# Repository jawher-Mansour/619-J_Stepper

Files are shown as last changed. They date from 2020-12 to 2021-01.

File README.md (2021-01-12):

<div align="center"><h1 style="font-family: courier;" align="center">619-J_Stepper</h1></div>
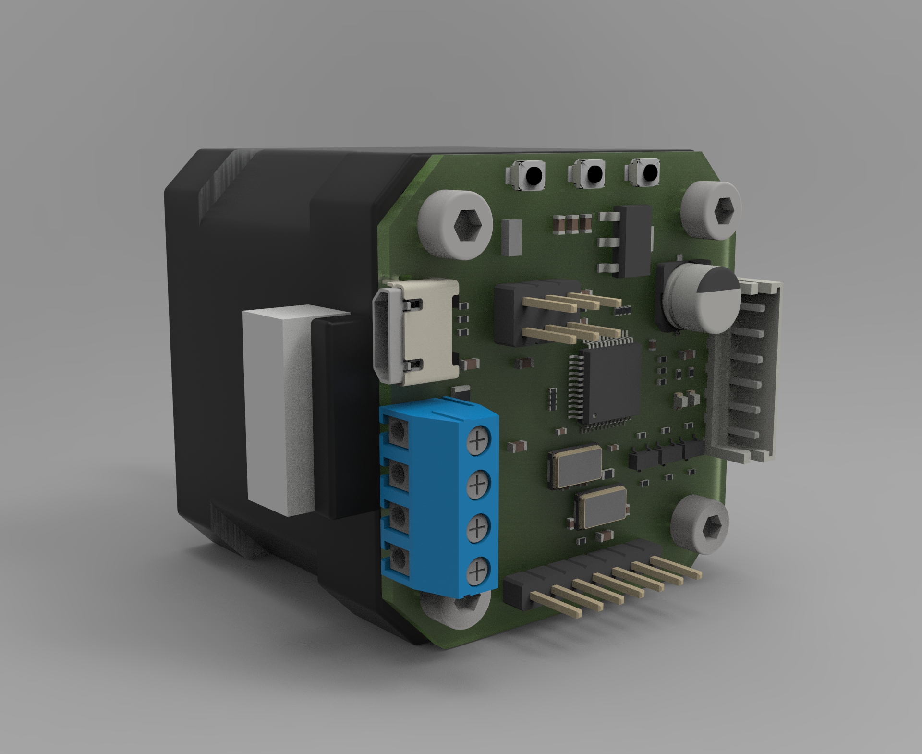
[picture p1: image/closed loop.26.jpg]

<div align="center"><b>An open source closed loop stepper driver.</b></div>

# 619-J_Stepper
**619-J_Stepper** is an open source micro-controller board used to drive a stepper motor in closed loop mode. The board is generally used on 3D printer steppers or CNC steppers to prevent losing steps. The project is inspired by [**Tropical labs: Mechaduino board**](https://tropical-labs.com/mechaduino/).

Here the **features** of the **619-J_Stepper**:

* **STM32F103C8T6 ARM 32-bit Cortex™-M3** is the CPU of the board. Higher frequency, higher speed and cost-effictive.  

* **Magnetic encoder to Allegro's A1333LLETR-T** Contactless 0° to 360° angle sensor IC ,12bit

* **USB programming** and **serial communication** (serial version)

* High speed printing without losing steps.

* Ported the compilation platform from arduino to PlatformIO —— Convenient for STM32 MCU compilation

* This project support build and upload by platformio, you can use Atom or Code editor (need install platformio) build it or upload firmware.

* Cosed loop motor feedback.

Here are the schematic and the board:

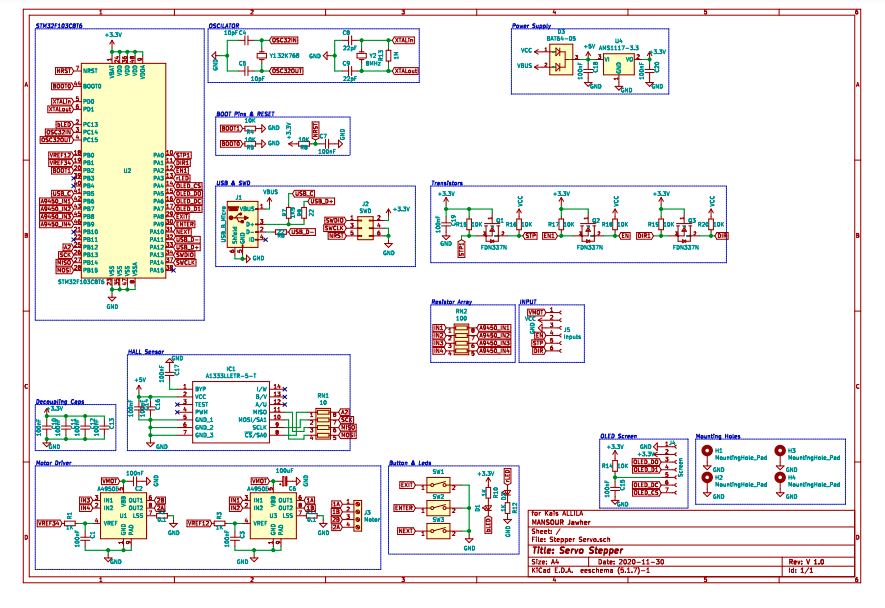
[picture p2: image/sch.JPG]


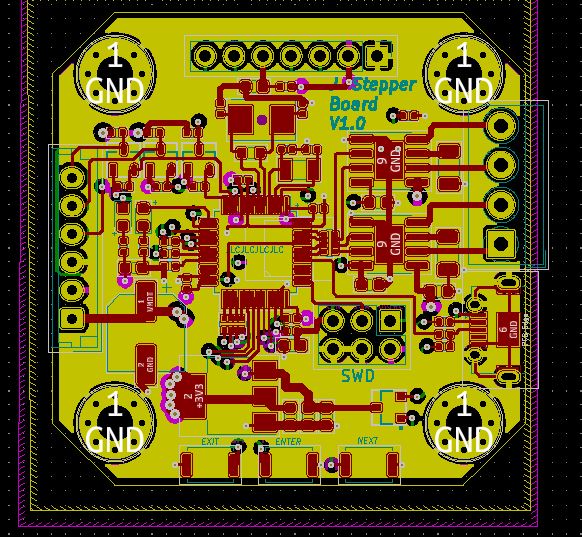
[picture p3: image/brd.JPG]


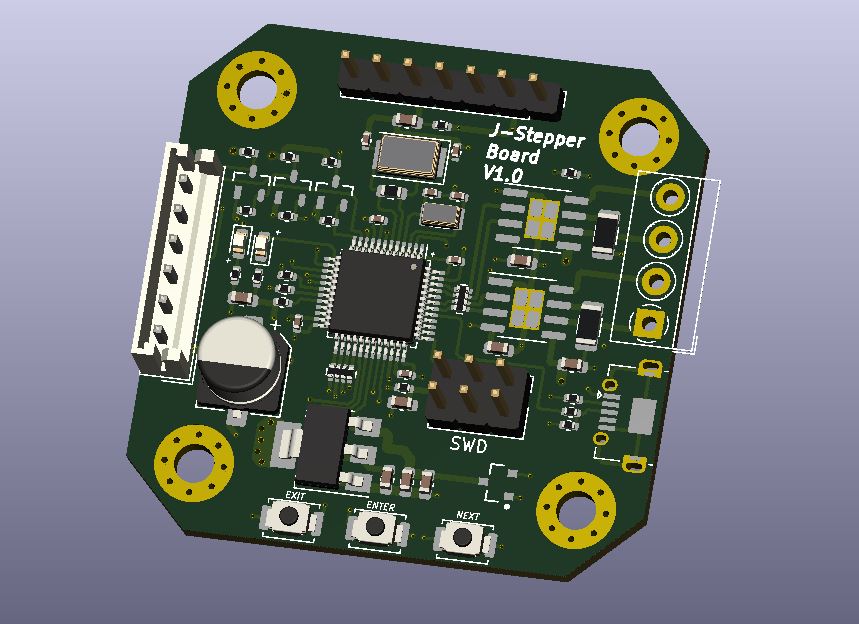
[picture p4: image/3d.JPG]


<iframe src="https://myhub.autodesk360.com/ue2824bfc/shares/public/SH919a0QTf3c32634dcfc82b0b883f1f9a82?mode=embed" width="640" height="480" allowfullscreen="true" webkitallowfullscreen="true" mozallowfullscreen="true"  frameborder="0"></iframe>

# Manufacturing

After finishing the Routing and verify the pcb. We made the board at **[JLC PCB](https://jlcpcb.com/)**  and we chose also the PCB Assembly service which was very good.

Here is the **[BOM needed](https://github.com/FAB619/619-J_Stepper/blob/main/files/BOM_final.xlsx)** for jlcpcb assembly service:

| Designator | Quantity | value | footprint | LCSC Part |
| --- | --- | --- | --- | --- |
| U2 | 1 | STM32F103C8T6 | Package\_QFP:LQFP-48\_7x7mm\_P0.5mm | C8734 |
| R4 | 1 | 10K | 0402 | C25744 |
| Y1 | 1 | 32K768 | Crystal:Crystal\_SMD\_3215-2Pin\_3.2x1.5mm | C252398 |
| C5 | 1 | 10pF | 0402 |  C32949 |
| C4 | 1 | 10pF | 0402 |  C32949 |
| Y2 | 1 | 8MHz | Crystal:Crystal\_SMD\_5032-2Pin\_5.0x3.2mm |  C115962 |
| C8 | 1 | 22pF | 0402 |  C1555 |
| C9 | 1 | 22pF | 0402 |  C1555 |
| R13 | 1 | 1M | 0603 | C22935 |
| C7 | 1 | 100nF | 0603 | C14663 |
| R5 | 1 | 10K | 0402 |  C25744 |
| R8 | 1 | 10K | 0402 |  C25744 |
| C10 | 1 | 100nF | 0402 | [ C1525](https://lcsc.com/product-detail/Multilayer-Ceramic-Capacitors-MLCC-SMD-SMT_SAMSUNG_CL05B104KO5NNNC_100nF-104-10-16V_C1525.html/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) |
| C11 | 1 | 100nF | 0402 | [ C1525](https://lcsc.com/product-detail/Multilayer-Ceramic-Capacitors-MLCC-SMD-SMT_SAMSUNG_CL05B104KO5NNNC_100nF-104-10-16V_C1525.html/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) |
| C12 | 1 | 100nF | 0402 | [ C1525](https://lcsc.com/product-detail/Multilayer-Ceramic-Capacitors-MLCC-SMD-SMT_SAMSUNG_CL05B104KO5NNNC_100nF-104-10-16V_C1525.html/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) |
| C13 | 1 | 100nF | 0402 | [ C1525](https://lcsc.com/product-detail/Multilayer-Ceramic-Capacitors-MLCC-SMD-SMT_SAMSUNG_CL05B104KO5NNNC_100nF-104-10-16V_C1525.html/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) |
| J1 | 1 | USB\_B\_Micro | Connector\_USB:USB\_Micro-AB\_Molex\_47590-0001 | C136001 |
| R9 | 1 | 22 | 0402 | [ C25092](https://lcsc.com/product-detail/Chip-Resistor-Surface-Mount_Uniroyal-Elec-0402WGF220JTCE_C25092.html/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) |
| R6 | 1 | 22 | 0402 | [ C25092](https://lcsc.com/product-detail/Chip-Resistor-Surface-Mount_Uniroyal-Elec-0402WGF220JTCE_C25092.html/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) |
| R7 | 1 | 1K5 | 0402 | [ C25867](https://lcsc.com/product-detail/Chip-Resistor-Surface-Mount_Uniroyal-Elec-0402WGF1501TCE_C25867.html/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) |
| D1 | 1 | LED | 0603 | [ C72041](https://lcsc.com/product-detail/Light-Emitting-Diodes-LED_0603-Blue-light_C72041.html/?href=jlc-SMT) |
| R10 | 1 | 1K | 0402 | [ C11702](https://lcsc.com/product-detail/Chip-Resistor-Surface-Mount_Uniroyal-Elec-0402WGF1001TCE_C11702.html/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) |
| D2 | 1 | LED\_Small | 0603 | [ C2286](https://lcsc.com/product-detail/Light-Emitting-Diodes-LED_Hubei-KENTO-Elec-KT-0603R_C2286.html/?href=jlc-SMT) |
| R12 | 1 | 1K | 0402 | [ C11702](https://lcsc.com/product-detail/Chip-Resistor-Surface-Mount_Uniroyal-Elec-0402WGF1001TCE_C11702.html/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) |
| SW1 | 1 | SW\_DIP\_x01  | Button\_Switch\_SMD:SW\_Push\_SPST\_NO\_Alps\_SKRK | [ C115357](https://lcsc.com/product-detail/Tactile-Switches_ALPS-Electric-SKRKAEE020_C115357.html/?href=jlc-SMT) |
| SW2 | 1 | SW\_DIP\_x01  | Button\_Switch\_SMD:SW\_Push\_SPST\_NO\_Alps\_SKRK | [ C115357](https://lcsc.com/product-detail/Tactile-Switches_ALPS-Electric-SKRKAEE020_C115357.html/?href=jlc-SMT) |
| SW3 | 1 | SW\_DIP\_x01  | Button\_Switch\_SMD:SW\_Push\_SPST\_NO\_Alps\_SKRK | [ C115357](https://lcsc.com/product-detail/Tactile-Switches_ALPS-Electric-SKRKAEE020_C115357.html/?href=jlc-SMT) |
| D3 | 1 | BAT64-05 | eec:Infineon-BAT64-05-Level\_C | C779239 |
| U4 | 1 | AMS1117-3.3 | Package\_TO\_SOT\_SMD:SOT-223-3\_TabPin2 | [ C6186](https://lcsc.com/product-detail/Low-Dropout-Regulators-LDO_AMS_AMS1117-3-3_AMS1117-3-3_C6186.html/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) |
| C18 | 1 | 100nF | 0603 | C14663 |
| C20 | 1 | 100nF | 0603 | C14663 |
| C15 | 1 | 100nF | 0603 | C14663 |
| R14 | 1 | 10K | 0402 |  C25744 |
| Q1 | 1 | FDN337N | FDN337N:ON\_Semi-527AG-01-12\_2008-O-IPC\_C | [ C475694](https://lcsc.com/product-detail/MOSFET_Shikues-FDN337N_C475694.html/?href=jlc-SMT) |
| R15 | 1 | 10K | 0402 |  C25744 |
| C19 | 1 | 100nF | 0603 | C14663 |
| R16 | 1 | 10K | 0402 |  C25744 |
| Q3 | 1 | FDN337N | FDN337N:ON\_Semi-527AG-01-12\_2008-O-IPC\_C | [ C475694](https://lcsc.com/product-detail/MOSFET_Shikues-FDN337N_C475694.html/?href=jlc-SMT) |
| R20 | 1 | 10K | 0402 |  C25744 |
| R19 | 1 | 10K | 0402 |  C25744 |
| Q2 | 1 | FDN337N | FDN337N:ON\_Semi-527AG-01-12\_2008-O-IPC\_C | [ C475694](https://lcsc.com/product-detail/MOSFET_Shikues-FDN337N_C475694.html/?href=jlc-SMT) |
| R18 | 1 | 10K | 0402 |  C25744 |
| R17 | 1 | 10K | 0402 |  C25744 |
| C17 | 1 | 100nF | 0603 | C14663 |
| C14 | 1 | 100nF | 0603 | C14663 |
| C16 | 1 | 100nF | 0603 | C14663 |
| RN1 | 1 | 10 | 0402 | [C25496](https://lcsc.com/product-detail/Resistor-Networks-Arrays_Uniroyal-Elec-4D02WGJ0100TCE_C25496.html/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) |
| RN2 | 1 | 100 | 0402 | [ C48442](https://lcsc.com/product-detail/Resistor-Networks-Arrays_Uniroyal-Elec-4D02WGJ0101TCE_C48442.html/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) |
| U1 | 1 | A4950E | Package\_SO:SOIC-8-1EP\_3.9x4.9mm\_P1.27mm\_EP2.41x3.3mm | [ C82404](https://lcsc.com/product-detail/Motor-Drivers_Allegro-MicroSystems-LLC_A4950ELJTR-T_Allegro-MicroSystems-LLC-A4950ELJTR-T_C82404.html/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) |
| R1 | 1 | 1K | 0402 | [ C11702](https://lcsc.com/product-detail/Chip-Resistor-Surface-Mount_Uniroyal-Elec-0402WGF1001TCE_C11702.html/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) |
| C1 | 1 | 100nF | 0603 | C14663 |
| R2 | 1 | 0.1 | 1206 | [ C25334](https://lcsc.com/product-detail/Chip-Resistor-Surface-Mount_Uniroyal-Elec-1206W4F100LT5E_C25334.html/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) |
| U3 | 1 | A4950E | Package\_SO:SOIC-8-1EP\_3.9x4.9mm\_P1.27mm\_EP2.41x3.3mm | [ C82404](https://lcsc.com/product-detail/Motor-Drivers_Allegro-MicroSystems-LLC_A4950ELJTR-T_Allegro-MicroSystems-LLC-A4950ELJTR-T_C82404.html/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) |
| C3 | 1 | 100nF | 0603 | C14663 |
| R3 | 1 | 1K | 0402 | [ C11702](https://lcsc.com/product-detail/Chip-Resistor-Surface-Mount_Uniroyal-Elec-0402WGF1001TCE_C11702.html/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) |
| R11 | 1 | 0.1 | 1206 | [ C25334](https://lcsc.com/product-detail/Chip-Resistor-Surface-Mount_Uniroyal-Elec-1206W4F100LT5E_C25334.html/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) |
| C6 | 1 | 100uF | SMD-ECAP-6.3x5.3 | [ C176682](https://lcsc.com/product-detail/Aluminum-Electrolytic-Capacitors-SMD_Lelon-VZH101M1CTR-0605_C176682.html/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) |
| C2 | 1 | 100nF | 0603 | C14663 |

# Downloads

* [619-J_Stepper schematics](https://github.com/FAB619/619-J_Stepper/tree/main/files/Kicad%20Files)

* [619-J_Stepper board](https://github.com/FAB619/619-J_Stepper/tree/main/files/Kicad%20Files)

* [619-J_Stepper Step](https://github.com/FAB619/619-J_Stepper/blob/main/files/Stepper%20Servo.step)

* [619-J_Stepper BOM](https://github.com/FAB619/619-J_Stepper/blob/main/files/BOM_final.xlsx)

* [619-J_Stepper Position file](https://github.com/FAB619/619-J_Stepper/blob/main/files/Stepper%20Servo-all-pos.csv)

* [619-J_Stepper Gerber](https://github.com/FAB619/619-J_Stepper/tree/main/files/Manufacturing)

# Getting started

# License

The hardware is under the Creative Commons Attribution Share-Alike 4.0 License as much of the work is based on Mechaduino project by J. Church.

<br />Ce(tte) œuvre est mise à disposition selon les termes de la <a rel="license" href="http://creativecommons.org/licenses/by-nc-sa/4.0/">Licence Creative Commons Attribution - Pas d’Utilisation Commerciale - Partage dans les Mêmes Conditions 4.0 International</a>.

# Disclaimer

This hardware/software is provided "as is", and you use the hardware/software at your own risk. Under no circumstances shall any author be liable for direct, indirect, special, incidental, or consequential damages resulting from the use, misuse, or inability to use this hardware/software, even if the authors have been advised of the possibility of such damages.

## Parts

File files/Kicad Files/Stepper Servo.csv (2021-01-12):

Comment | Designator | Footprint | LCSC Part #
100nF Unpolarized capacitor, small symbol | C1,C2,C3,C7,C14,C15,C16,C17,C18,C19,C20 | C_0603_1608Metric
10pF Unpolarized capacitor, small symbol | C4,C5 | C_0402_1005Metric
100uF Polarized capacitor, small symbol | C6 | CP_Elec_5x5.3
22pF Unpolarized capacitor, small symbol | C8,C9 | C_0402_1005Metric
100nF Unpolarized capacitor, small symbol | C10,C11,C12,C13 | C_0402_1005Metric
LED Light emitting diode, small symbol | D1 | LED_0603_1608Metric
LED_Small Light emitting diode, small symbol | D2 | LED_0603_1608Metric
BAT64-05 BAT64-05 | D3 | Infineon-BAT64-05-Level_C
MountingHole_Pad Mounting Hole with connection | H1,H2,H3,H4 | MountingHole_3.2mm_M3_Pad_Via
A1333LLETR-5-T A1333LLETR-5-T | IC1 | SOP65P640X125-14N
USB_B_Micro USB Micro Type B connector | J1 | USB_Micro-AB_Molex_47590-0001
SWD Generic connector, double row, 02x03, odd/even pin numbering scheme (row 1 odd numbers, row 2 even numbers), script generated (kicad-library-utils/schlib/autogen/connector/) | J2 | PinHeader_2x03_P2.54mm_Vertical
Motor Generic screw terminal, single row, 01x04, script generated (kicad-library-utils/schlib/autogen/connector/) | J3 | TerminalBlock_MetzConnect_Type059_RT06304HBWC_1x04_P3.50mm_Horizontal
Screen Generic connector, single row, 01x07, script generated (kicad-library-utils/schlib/autogen/connector/) | J4 | PinHeader_1x07_P2.54mm_Vertical
Inputs Generic connector, single row, 01x06, script generated (kicad-library-utils/schlib/autogen/connector/) | J5 | JST_EH_B6B-EH-A_1x06_P2.50mm_Vertical
FDN337N FDN337N | Q1,Q2,Q3 | ON_Semi-527AG-01-12_2008-O-IPC_C
1K Resistor, small symbol | R1,R3,R10,R12 | R_0402_1005Metric
0.1 Resistor, small symbol | R2,R11 | R_1206_3216Metric
10K Resistor, small symbol | R4,R5,R8,R14,R15,R16,R17,R18,R19,R20 | R_0402_1005Metric
22 Resistor, small symbol | R6,R9 | R_0402_1005Metric
1K5 Resistor, small symbol | R7 | R_0402_1005Metric
1M Resistor, small symbol | R13 | R_0603_1608Metric
10 4 resistor network, parallel topology | RN1 | R_Array_Convex_4x0402
100 4 resistor network, parallel topology | RN2 | R_Array_Convex_4x0402
SW_DIP_x01 1x DIP Switch, Single Pole Single Throw (SPST) switch, small symbol | SW1,SW2,SW3 | SW_Push_SPST_NO_Alps_SKRK
A4950E Full-Bridge, DMOS PWM, Motor Driver, 40V, 3.5A, -40 to +85C | U1,U3 | SOIC-8-1EP_3.9x4.9mm_P1.27mm_EP2.41x3.3mm
STM32F103C8T6 ARM Cortex-M3 MCU, 64KB flash, 20KB RAM, 72MHz, 2-3.6V, 37 GPIO, LQFP-48 | U2 | LQFP-48_7x7mm_P0.5mm
AMS1117-3.3 1A Low Dropout regulator, positive, 3.3V fixed output, SOT-223 | U4 | SOT-223-3_TabPin2
32K768 Two pin crystal, small symbol | Y1 | Crystal_SMD_3215-2Pin_3.2x1.5mm
8MHz Two pin crystal, small symbol | Y2 | Crystal_SMD_5032-2Pin_5.0x3.2mm

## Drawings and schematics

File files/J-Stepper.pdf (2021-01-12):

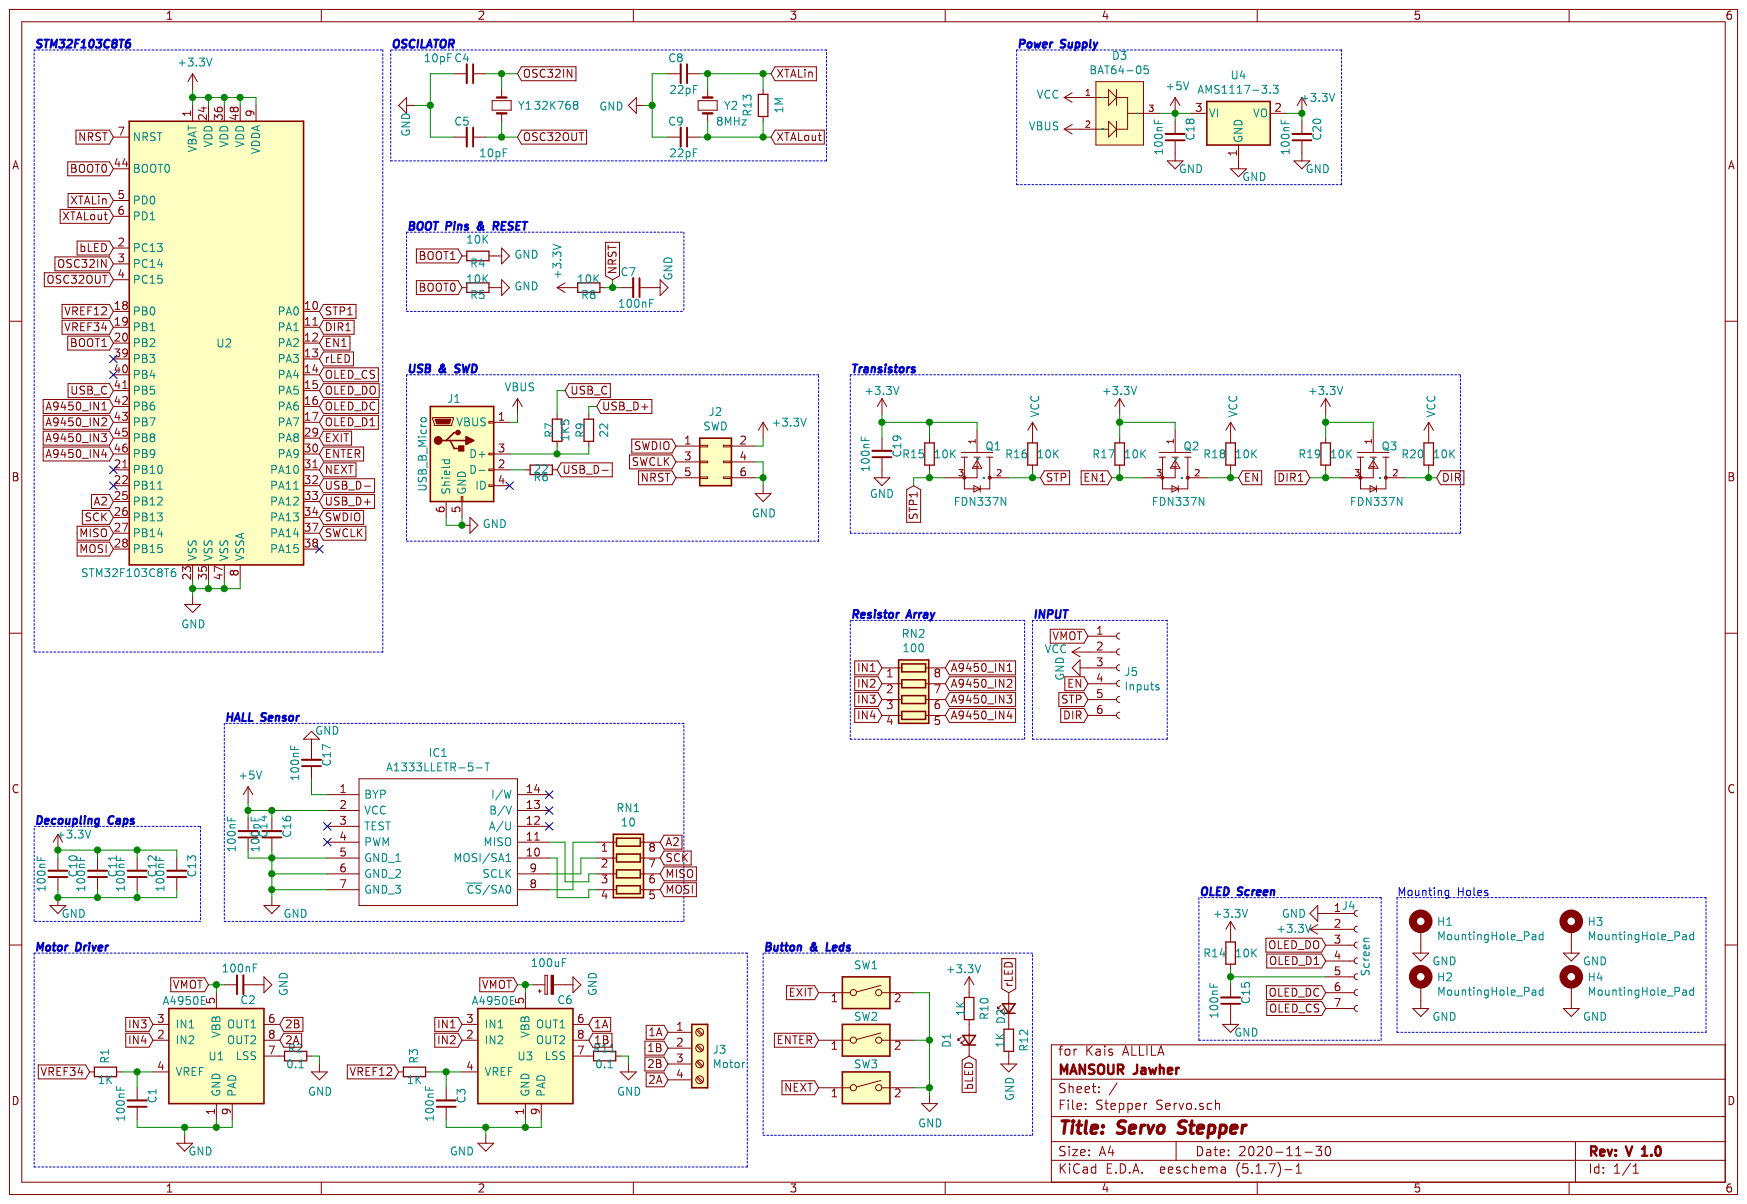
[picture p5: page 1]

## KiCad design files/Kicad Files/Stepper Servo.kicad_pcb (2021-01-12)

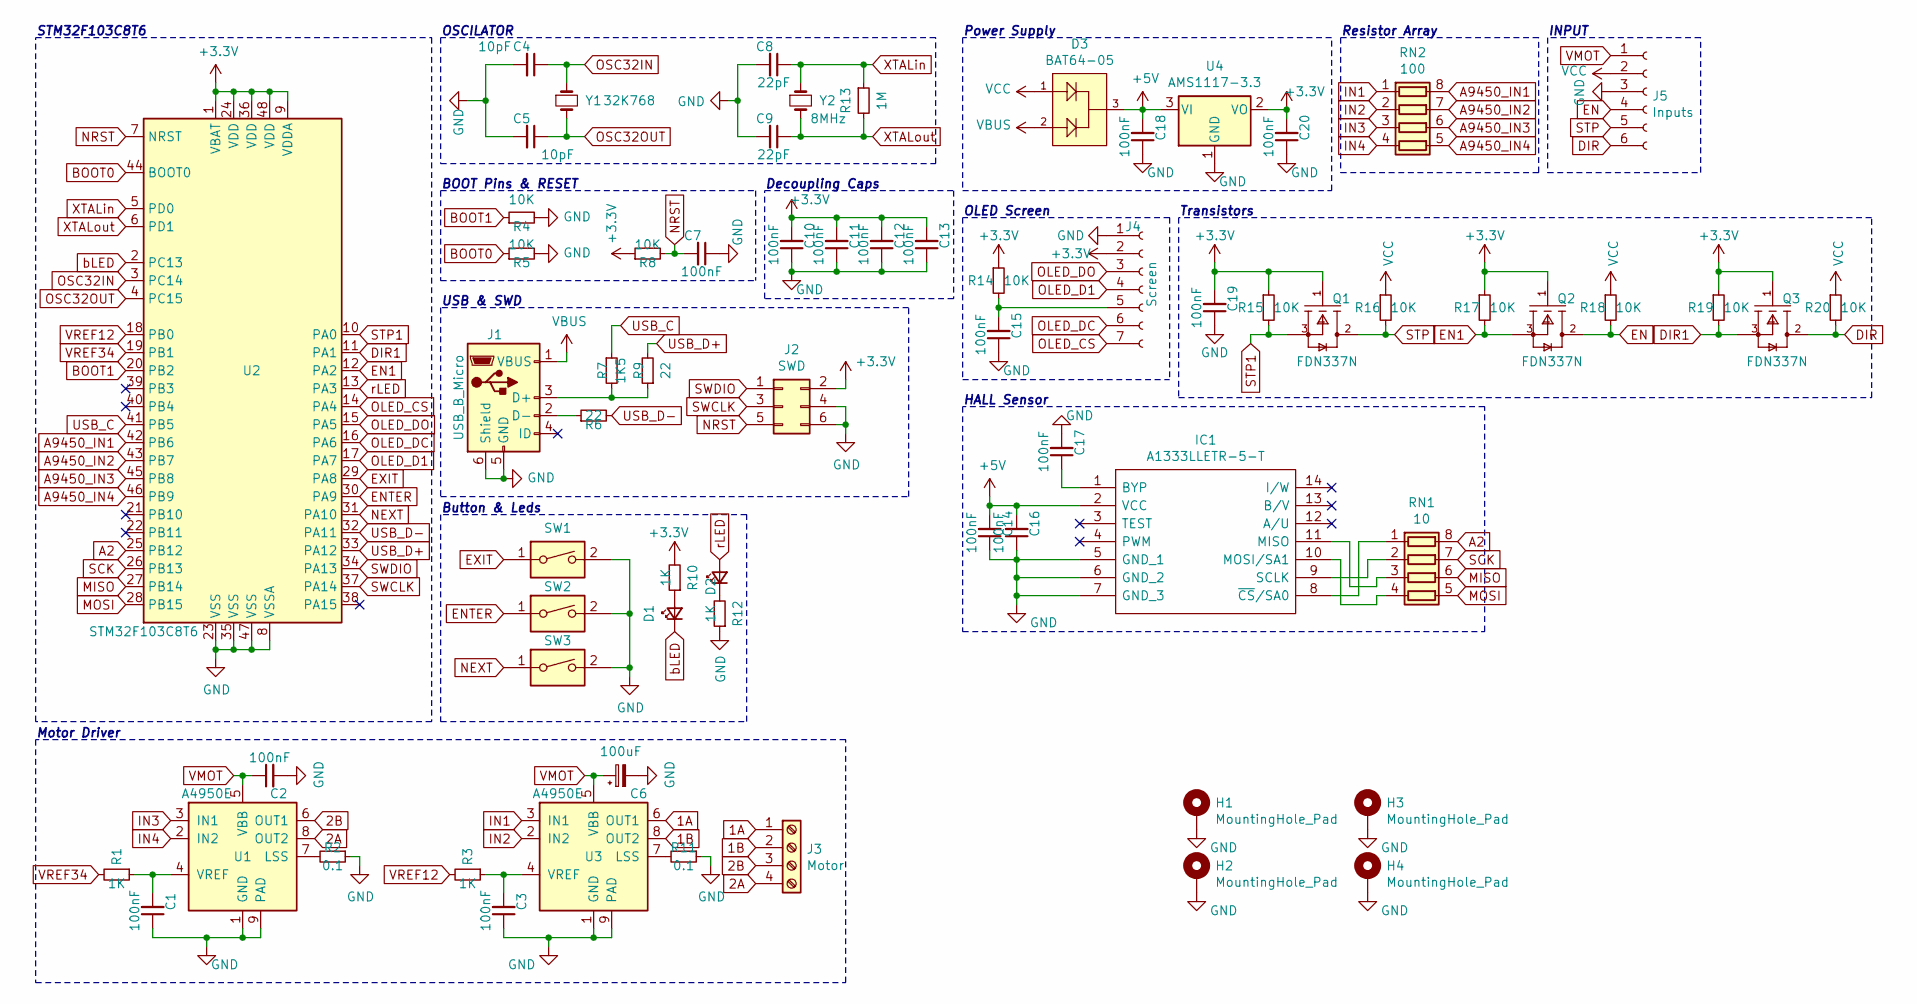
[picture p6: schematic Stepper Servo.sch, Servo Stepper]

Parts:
C1, C2, C3, C7, C14, C15, C16, C17, C18, C19, C20: 100nF; C_0603_1608Metric
C4, C5: 10pF; C_0402_1005Metric
C6: 100uF; CP_Elec_5x5.3
C8, C9: 22pF; C_0402_1005Metric
C10, C11, C12, C13: 100nF; C_0402_1005Metric
D1: LED; LED_0603_1608Metric
D2: LED_Small; LED_0603_1608Metric
D3: BAT64-05; Infineon-BAT64-05-Level_C
H1, H2, H3, H4: MountingHole_Pad; MountingHole_3.2mm_M3_Pad_Via
IC1: A1333LLETR-5-T; SOP65P640X125-14N; Manufacturer_Part_Number A1333LLETR-5-T
J1: USB_B_Micro; USB_Micro-AB_Molex_47590-0001
J2: SWD; PinHeader_2x03_P2.54mm_Vertical
J3: Motor; TerminalBlock_MetzConnect_Type059_RT06304HBWC_1x04_P3.50mm_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
J4: Screen; PinHeader_1x07_P2.54mm_Vertical
J5: Inputs; JST_EH_B6B-EH-A_1x06_P2.50mm_Vertical
Q1, Q2, Q3: FDN337N; ON_Semi-527AG-01-12_2008-O-IPC_C; mouser part number 512-FDN337N; digikey description MOSFET N-CH 30V 2.2A SSOT3
R1, R3, R10, R12: 1K; R_0402_1005Metric
R2, R11: 0.1; R_1206_3216Metric
R4, R5, R8, R14, R15, R16, R17, R18, R19, R20: 10K; R_0402_1005Metric
R6, R9: 22; R_0402_1005Metric
R7: 1K5; R_0402_1005Metric
R13: 1M; R_0603_1608Metric
RN1: 10; R_Array_Convex_4x0402
RN2: 100; R_Array_Convex_4x0402
SW1, SW3: SW_DIP_x01; SW_Push_SPST_NO_Alps_SKRK
SW2: SW_DIP_x01; SW_Push_SPST_NO_Alps_SKRK; LCSC C455280
U1, U3: A4950E; SOIC-8-1EP_3.9x4.9mm_P1.27mm_EP2.41x3.3mm
U2: STM32F103C8T6; LQFP-48_7x7mm_P0.5mm
U4: AMS1117-3.3; SOT-223-3_TabPin2
Y1: 32K768; Crystal_SMD_3215-2Pin_3.2x1.5mm
Y2: 8MHz; Crystal_SMD_5032-2Pin_5.0x3.2mm

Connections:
1A: J3.1, U3.6 (OUT1)
1B: J3.2, U3.8 (OUT2)
2A: J3.4, U1.8 (OUT2)
2B: J3.3, U1.6 (OUT1)
+3V3: C10.2, C11.2, C12.2, C13.2, C19.2, C20.2, J2.2, J4.2, Q1.1 (G), Q2.1 (G), Q3.1 (G), R8.1, R10.2, R14.1, R15.1, R17.1, R19.1, U2.1 (VBAT), U2.9 (VDDA), U2.24 (VDD), U2.36 (VDD), U2.48 (VDD), U4.2 (VO)
+5V: C14.2, C16.2, C18.2, D3.3 (K), IC1.2 (VCC), U4.3 (VI)
A2: RN1.8 (R1.2), U2.25 (PB12)
A9450_IN1: RN2.8 (R1.2), U2.42 (PB6)
A9450_IN2: RN2.7 (R2.2), U2.43 (PB7)
A9450_IN3: RN2.6 (R3.2), U2.45 (PB8)
A9450_IN4: RN2.5 (R4.2), U2.46 (PB9)
BOOT0: R5.1, U2.44 (BOOT0)
BOOT1: R4.1, U2.20 (PB2)
DIR: J5.6, Q3.2 (D), R20.2
DIR1: Q3.3 (S), R19.2, U2.11 (PA1)
EN: J5.4, Q2.2 (D), R18.2
EN1: Q2.3 (S), R17.2, U2.12 (PA2)
ENTER: SW2.1, U2.30 (PA9)
EXIT: SW1.1, U2.29 (PA8)
GND: C1.1, C2.2, C3.1, C4.2, C5.2, C6.2, C7.1, C8.2, C9.2, C10.1, C11.1, C12.1, C13.1, C14.1, C15.1, C16.1, C17.2, C18.1, C19.1, C20.1, H1.1, H2.1, H3.1, H4.1, IC1.5 (GND_1), IC1.6 (GND_2), IC1.7 (GND_3), J1.5 (GND), J1.6 (Shield), J2.4, J2.6, J4.1, J5.3, R2.1, R4.2, R5.2, R11.1, R12.1, SW1.2, SW2.2, SW3.2, U1.1 (GND), U1.9 (PAD), U2.8 (VSSA), U2.23 (VSS), U2.35 (VSS), U2.47 (VSS), U3.1 (GND), U3.9 (PAD), U4.1 (GND)
IN1: RN2.1 (R1.1), U3.3 (IN1)
IN2: RN2.2 (R2.1), U3.2 (IN2)
IN3: RN2.3 (R3.1), U1.3 (IN1)
IN4: RN2.4 (R4.1), U1.2 (IN2)
MISO: RN1.6 (R3.2), U2.27 (PB14)
MOSI: RN1.5 (R4.2), U2.28 (PB15)
NEXT: SW3.1, U2.31 (PA10)
NRST: C7.2, J2.5, R8.2, U2.7 (NRST)
unnamed: C1.2, R1.1, U1.4 (VREF)
unnamed: C3.2, R3.1, U3.4 (VREF)
unnamed: C15.2, J4.5, R14.2
unnamed: C17.1, IC1.1 (BYP)
unnamed: D1.2 (A), R10.1
unnamed: D2.1 (K), R12.2
unnamed: IC1.8 (~CS~/SA0), RN1.1 (R1.1)
unnamed: IC1.9 (SCLK), RN1.2 (R2.1)
unnamed: IC1.10 (MOSI/SA1), RN1.4 (R4.1)
unnamed: IC1.11 (MISO), RN1.3 (R3.1)
unnamed: J1.2 (D-), R6.1
unnamed: J1.3 (D+), R7.2, R9.1
unnamed: R2.2, U1.7 (LSS)
unnamed: R11.2, U3.7 (LSS)
OLED_CS: J4.7, U2.14 (PA4)
OLED_D1: J4.4, U2.17 (PA7)
OLED_DC: J4.6, U2.16 (PA6)
OLED_DO: J4.3, U2.15 (PA5)
OSC32IN: C4.1, U2.3 (PC14), Y1.1
OSC32OUT: C5.1, U2.4 (PC15), Y1.2
SCK: RN1.7 (R2.2), U2.26 (PB13)
STP: J5.5, Q1.2 (D), R16.2
STP1: Q1.3 (S), R15.2, U2.10 (PA0)
SWCLK: J2.3, U2.37 (PA14)
SWDIO: J2.1, U2.34 (PA13)
USB_C: R7.1, U2.41 (PB5)
USB_D+: R9.2, U2.33 (PA12)
USB_D-: R6.2, U2.32 (PA11)
VBUS: D3.2 (A2), J1.1 (VBUS)
VCC: D3.1 (A1), J5.2, R16.1, R18.1, R20.1
VMOT: C2.1, C6.1, J5.1, U1.5 (VBB), U3.5 (VBB)
VREF12: R3.2, U2.18 (PB0)
VREF34: R1.2, U2.19 (PB1)
XTALin: C8.1, R13.1, U2.5 (PD0), Y2.1
XTALout: C9.1, R13.2, U2.6 (PD1), Y2.2
bLED: D1.1 (K), U2.2 (PC13)
rLED: D2.2 (A), U2.13 (PA3)

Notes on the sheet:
STM32F103C8T6
OSCILATOR
BOOT Pins & RESET
Decoupling Caps
USB & SWD
Button & Leds
Power Supply
OLED Screen
Transistors
HALL Sensor
Resistor Array
Motor Driver
INPUT

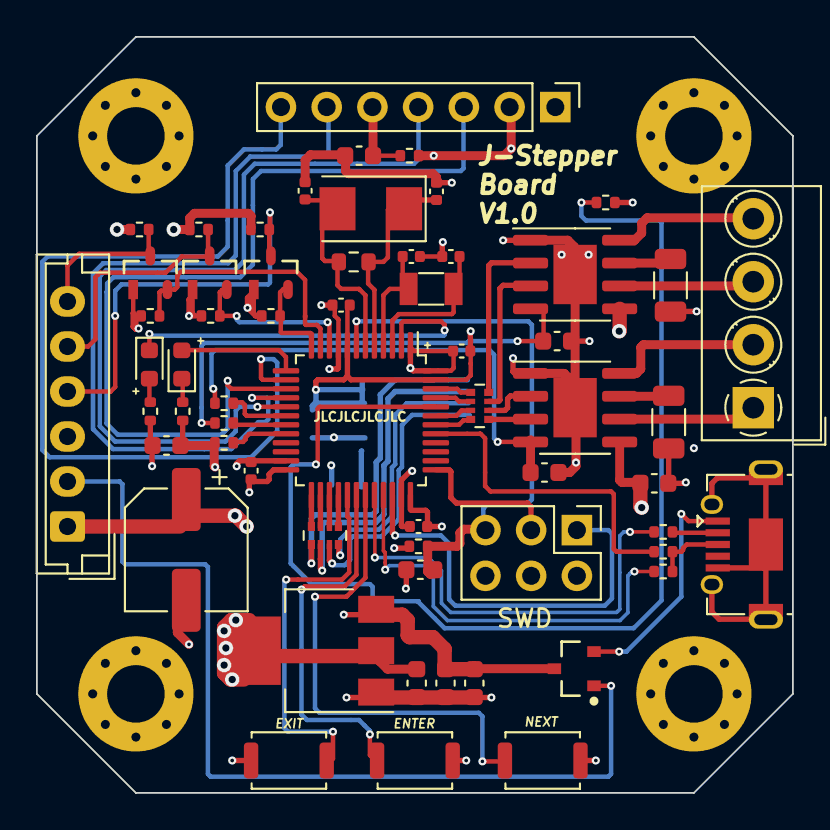
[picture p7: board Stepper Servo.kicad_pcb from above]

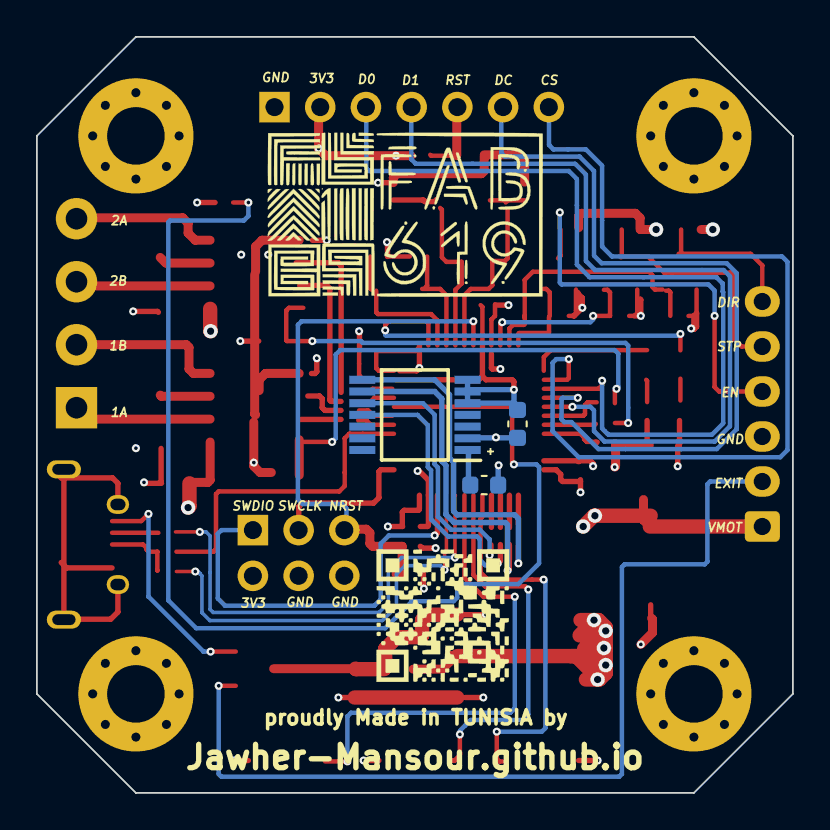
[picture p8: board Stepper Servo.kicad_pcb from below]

Board: 4 copper layers, 42.0 x 42.0 mm, 67 parts (3 on the bottom side), 65 nets.

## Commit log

2021-01-12 upload BOM
    [BOM_final.xlsx]
2021-01-12 upload pos file
    [Stepper Servo-all-pos.csv]
2021-01-12 Upload manufacturing files
    [Stepper Servo-B_Cu.gbr, Stepper Servo-B_Mask.gbr, Stepper Servo-B_Paste.gbr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]
2021-01-12 upload kicad files
    [Stepper Servo.csv, Stepper Servo.kicad_pcb, Stepper Servo.sch]
